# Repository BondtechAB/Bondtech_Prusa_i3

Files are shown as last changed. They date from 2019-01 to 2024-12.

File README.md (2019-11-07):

# Bondtech_Prusa_i3
Bondtech extruder upgrade for Prusa i3 printer uses 3:1 gearing ratio for improved precision and resolution, optimized geometry for the heat-sink cooling and many other improved features. With lower weight it also reduce vibrations and ghosting.

### Links
* Bondtech's Website: https://bondtech.se/en
* Assembly manual: https://support.bondtech.se/c/Prusa

### Contributors
This project was a Co-development with people from the Prusa community that have provided excellent feedback and suggestions of how to develop the "perfect" extruder setup for the Prusa series printer.

Special thanks to these aweome people! 
* Chris Warkocki
* Grégorie Saunier: https://github.com/gregsaun 
* Olof Ogland 
* Erik Bjorgan 
* Josh Jones 
* Kyle Wiehe 
* Marc Evertz 
* Matt Harrison 
* Ocie Ward
* Sando Bendig 
* Vecko Kojchevski 
* Steven Mölby

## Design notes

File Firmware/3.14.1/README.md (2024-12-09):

# 3.14.1 Firmware for Bondtech Prusa i3 MK25 / MK3,  MK25s / MK3s and MK25s / MK3s Mosquito

2024-12-09

Compiled firmware to support Bondtech Prusa i3 MK25 / MK3, MK25s / MK3s, MK25s / MK3s Mosquito and Bondtech LGX for MK3s & Mosquito

Firmware based on Prusa's latest release with adjustments to support bondtech extruders. Please read Prusa's release note for all changes in the new release: https://github.com/prusa3d/Prusa-Firmware/releases/tag/v3.14.1

# 3.14.1 Summary Bondtech specific changes

- Adjusted Load/Unload filament sequence.
- MK3/MK3s: Variants for Slice Engineering's High temperature thermistor (SE_HT-thermistor), E3DRevo.
- MK3/MK3s: Changed microstep resolution to 16.
- MK3s/MK25s: Correct Z_MAX_POS adjustments to allow XYZ Calibration.
- Full speed enabled for custom fans.

Source Code: https://github.com/BondtechAB/Bondtech-Prusa-Firmware

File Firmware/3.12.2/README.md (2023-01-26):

# 3.12.1 Firmware for Bondtech Prusa i3 MK25 / MK3,  MK25s / MK3s and MK25s / MK3s Mosquito

2023-01-26

Compiled firmware to support Bondtech Prusa i3 MK25 / MK3, MK25s / MK3s, MK25s / MK3s Mosquito and Bondtech LGX for MK3s & Mosquito

Firmware based on Prusa's latest release with adjustments to support bondtech extruders. Please read Prusa's release note for all changes in the new release: https://github.com/prusa3d/Prusa-Firmware/releases/tag/v3.12.1

# 3.12.1 Summary Bondtech specific changes

- Adjusted Load/Unload filament sequence.
- MK3/MK3s: Variants for Slice Engineering's High temperature thermistor (SE_HT-thermistor).
- MK3/MK3s: Changed microstep resolution to 16.
- MK3s/MK25s: Correct Z_MAX_POS adjustments to allow XYZ Calibration.
- MK3s/Mk25s: Adjusted mmu.cpp to correct values for E3Dv6, Mosquito and Mosquito Magnum together with the Bondtech extruder when preforming can_load and mmu_load_to_nozzle.
- Full speed enabled for custom fans.

Source Code: https://github.com/BondtechAB/Bondtech-Prusa-Firmware

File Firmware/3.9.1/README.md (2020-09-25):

# 3.9.1 Firmware for Bondtech Prusa i3 MK25 / MK3,  MK25s / MK3s and MK25s / MK3s Mosquito

2020-09-25

Compiled firmware to support Bondtech Prusa i3 MK25 / MK3, MK25s / MK3s, MK25s / MK3s Mosquito

Firmware based on Prusa's latest release with adjustments to support bondtech extruders. Please read Prusa's release note for all changes in the new release: https://github.com/prusa3d/Prusa-Firmware/releases/tag/v3.9.1

# 3.9.1 Summary Bondtech specific changes

- Variants for Slice Engineering's High temperature thermistor (SE_HT-thermistor).
- Adjusted Load/Unload filament sequence.
- MK3/MK3s: Changed microstep resolution to 16.
- MK3s/MK25s: Correct Z_MAX_POS adjustemts to allow XYZ Calibration.
- MK3s/Mk25s: Adjusted mmu.cpp to correct values for E3Dv6, Mosquito and Mosquito Magnum together with the Bondtech extruder when preforming can_load and mmu_load_to_nozzle.
- Now with multi language support.
- Full speed enabled for custom fans.

Source Code: https://github.com/BondtechAB/Bondtech-Prusa-Firmware

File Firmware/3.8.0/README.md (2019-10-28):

# 3.8.0 Firmware for Bondtech Prusa i3 MK25 / MK3,  MK25s / MK3s and MK25s / MK3s Mosquito

2019-09-11

Compiled firmware to support Bondtech Prusa i3 MK25s / MK3s, MK25s / MK3s Mosquito

# Summery Bondtech specific changes

- Variants for Slice Engineerings High temperature thermistor (SE_HT-thermistor)
- Adjusted Load/Unload filament sequence
- MK3/MK3s: Changed mirostep resolution to 16
- MK3s/MK25s: Changed Z_MAX_POS 205 to allow Z and XYZ calibration

##  MK3s Changes

- #define CUSTOM_MENDEL_NAME "Bondtech-PE MK3s"
- #define DEFAULT_AXIS_STEPS_PER_UNIT   {100,100,3200/8,415}
- #define Z_MAX_POS 205
- #define TMC2130_USTEPS_E    16    
- #define LOAD_FILAMENT_1 "G1 E80 F400"
- #define UNLOAD_FILAMENT_1 "G1 E-95 F7000"
- #define FILAMENTCHANGE_FINALRETRACT -95
- #define FILAMENTCHANGE_FIRSTFEED 80  

## MK3 Changes

- #define CUSTOM_MENDEL_NAME "Bondtech-PE MK3"
- #define DEFAULT_AXIS_STEPS_PER_UNIT   {100,100,3200/8,415}
- #define TMC2130_USTEPS_E    16
- #define LOAD_FILAMENT_1 "G1 E80 F400"
- #define UNLOAD_FILAMENT_1 "G1 E-95 F7000"
- #define FILAMENTCHANGE_FINALRETRACT -95
- #define FILAMENTCHANGE_FIRSTFEED 80

##  MK25s Changes

- #define CUSTOM_MENDEL_NAME "Bondtech-PE MK2.5S"
- #define DEFAULT_AXIS_STEPS_PER_UNIT   {100,100,3200/8,415}
- #define LOAD_FILAMENT_1 "G1 E80 F400"
- #define UNLOAD_FILAMENT_1 "G1 E-95 F7000"
- #define FILAMENTCHANGE_FINALRETRACT -95
- #define FILAMENTCHANGE_FIRSTFEED 80

## MK25 Changes

- #define CUSTOM_MENDEL_NAME "Bondtech-PE MK2.5"
- #define DEFAULT_AXIS_STEPS_PER_UNIT   {100,100,3200/8,415}
- #define LOAD_FILAMENT_1 "G1 E80 F400"
- #define UNLOAD_FILAMENT_1 "G1 E-95 F7000"
- #define FILAMENTCHANGE_FINALRETRACT -95
- #define FILAMENTCHANGE_FIRSTFEED 80

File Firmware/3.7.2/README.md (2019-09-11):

# bondtech_fw_MK3S_3_7_2.hex for MK3s

2019-07-12

Compiled firmware to support Bondtech Prusa i3 MK3s.

# Bondtech specific changes
1. Estep set to 830.
2. Z_MAX_POS 204 to allow Z and XYZ calibration.
3. Changed printer name.

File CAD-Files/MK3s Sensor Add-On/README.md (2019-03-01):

You can find the assembly manual here.

https://github.com/BondtechAB/Bondtech_Prusa_i3/blob/master/Doc/Sensor%20Add-On%20V1.0.pdf

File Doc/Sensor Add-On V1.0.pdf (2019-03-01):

# Sensor Add-On for Bondtech Prusa i3

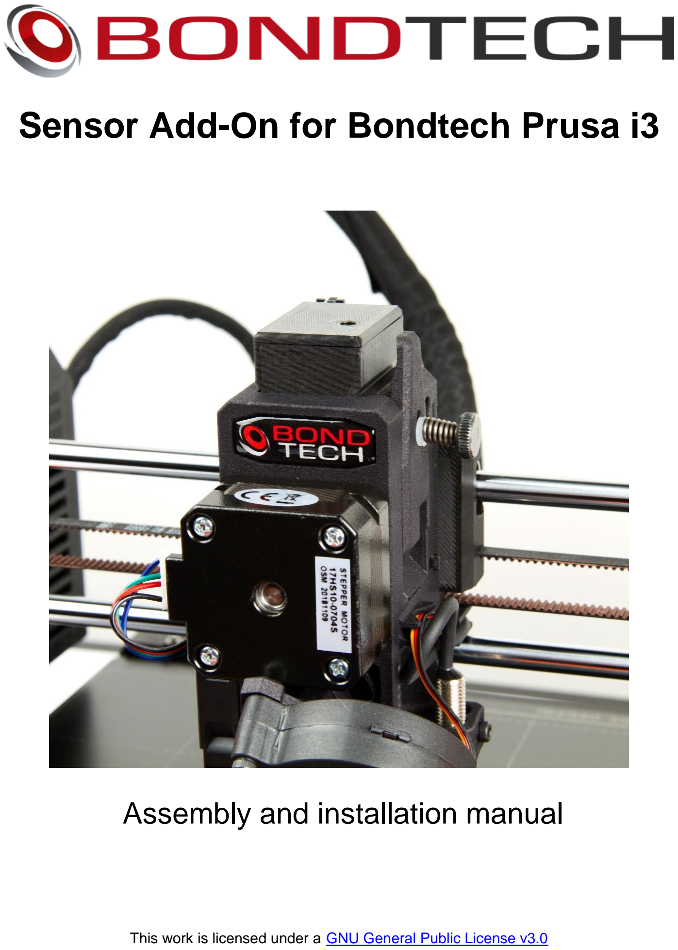
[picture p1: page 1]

## Assembly and installation manual

This work is licensed under a GNU General Public License v3.0 (https://www.gnu.org/licenses/gpl-3.0.html)

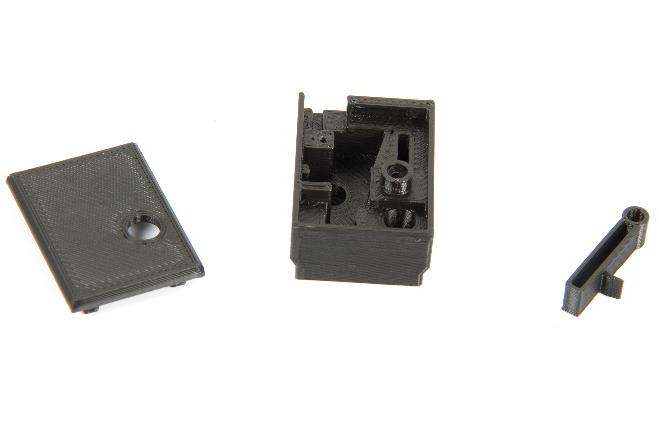
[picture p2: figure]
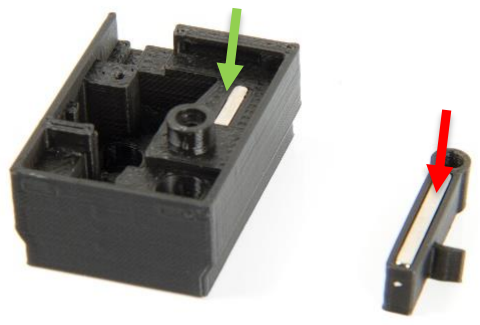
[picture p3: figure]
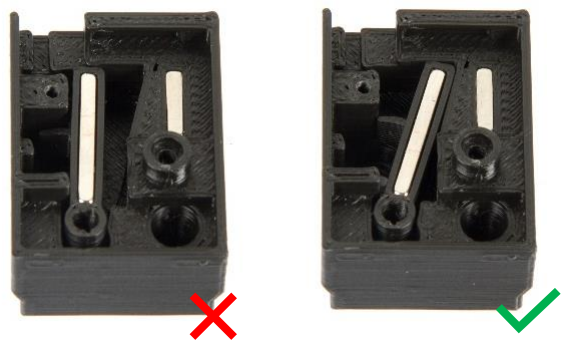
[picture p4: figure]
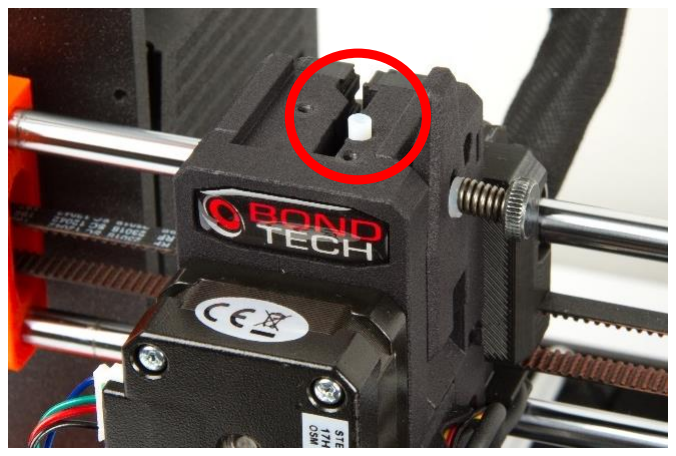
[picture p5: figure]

Installation of Sensor Add-On for Bondtech_Prusa_i3 V1.0 | 1
- Preparation. Download and print the lever, housing and cover from our GitHub page.
https://github.com/BondtechAB/Bondtech_Prusa_i3/tree/master/C AD-Files (https://github.com/BondtechAB/Bondtech_Prusa_i3/tree/master/CAD-Files)
- Recommended to print the lever with extra flow if the magnet is loose in the pocket.
- Insert the magnet. Make sure the 20x6x2 magnet is securely held in the lever.
- 20x6x2 magnet
- 10x6x2 magnet
- Ensure the magnets are
attracting each other.
- Remove your old sensor cover.
- Cut your old PTFE tube 6,5mm, chamfer the inside and insert it into the extruder body.

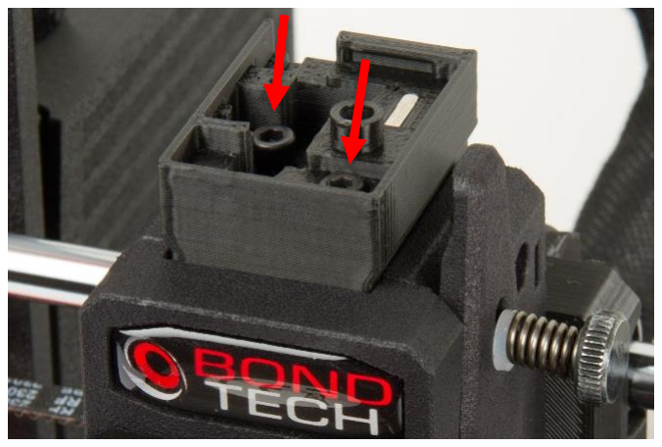
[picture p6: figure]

- Insert the new sensor housing in the slot and secure it using two M3x8 screws.
- M3x8

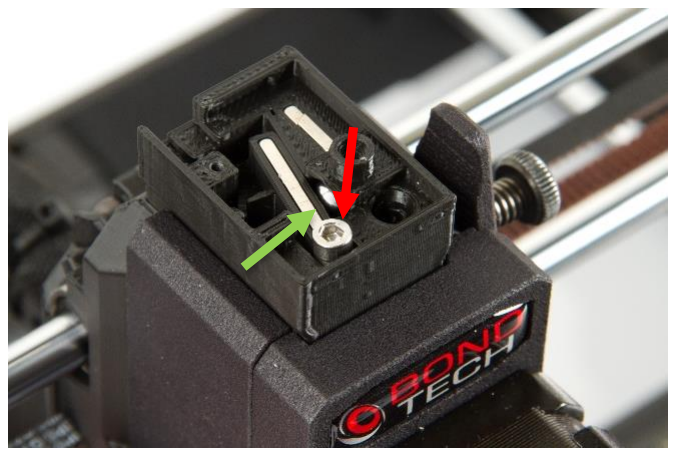
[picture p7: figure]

- Insert the steel ball and lever. Secure the lever using a M3x10 screw from your upgrade kit. (Make sure the lever can move freely)
- Steel ball
- M3x10

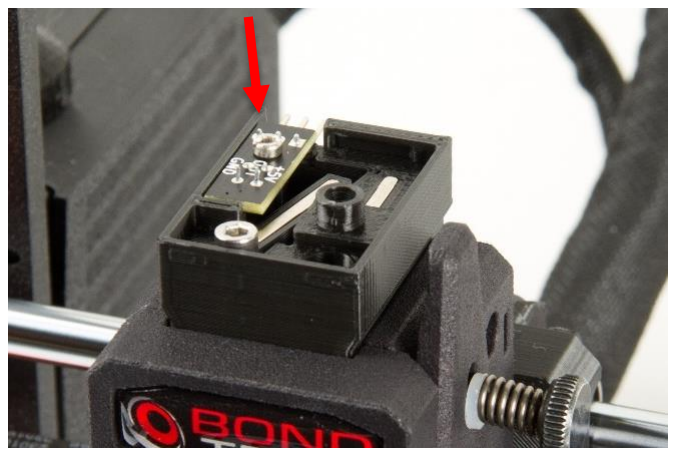
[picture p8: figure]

- Place and secure the sensor with a M2x8 screw delivered in your MK3s upgrade kit.
- M2x8

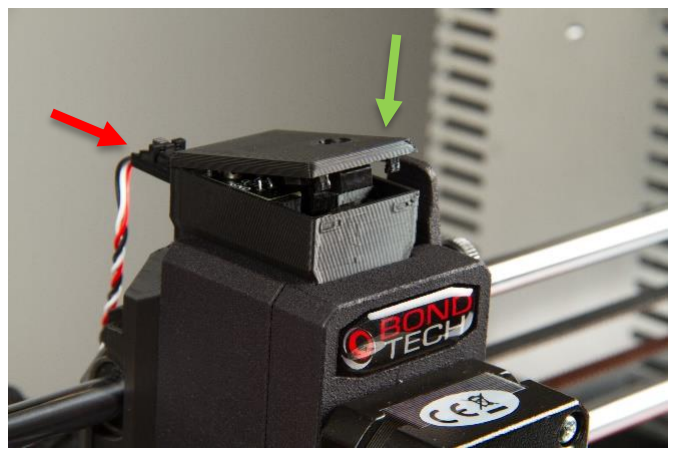
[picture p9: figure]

- Slide the lid back and carefully push it down in the front.
- Connect the wire to the sensor.

Good luck with your Bondtech feeder!

If you have any questions please first read the FAQ (http://www.bondtech.se/en/faq/). If the question still hasn’t been answered feel free to contact us by email or our online chat.

Repslagarvägen 3 J
33153 Värnamo
Sweden

e-mail: support@bondtech.se phone: +46702220193
paypal: payments@bondtech.se
web: www.bondtech.se
VAT-registration number: SE556995564301

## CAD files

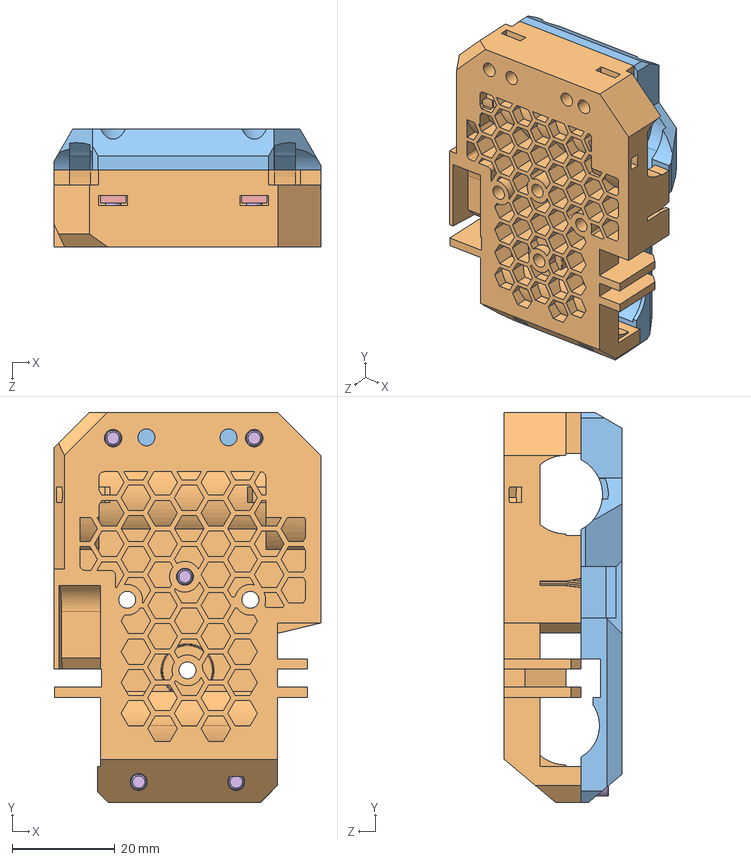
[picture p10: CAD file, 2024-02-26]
CAD-Files/Bondtech LGX for MK3S & Mosquito/LGX X-carriage for MK3S & Mosquito.STEP
52.0 x 76.0 x 22.9 mm
FKM Fyrkantsmutter_FKM2.5 x 5
MC6S_M3X10OBEH x 5

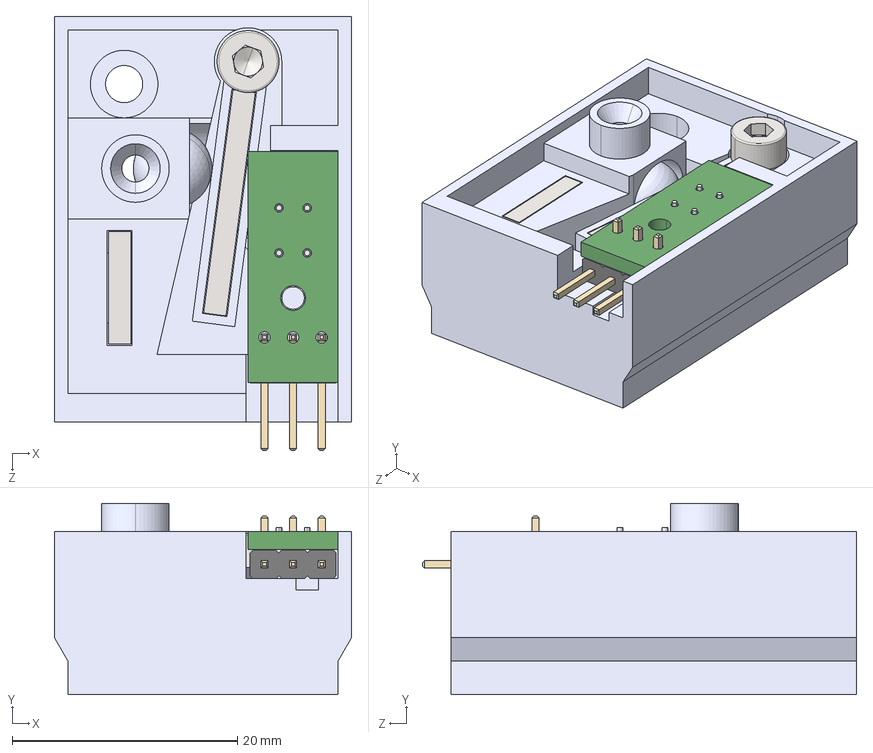
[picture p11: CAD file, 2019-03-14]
CAD-Files/MK3s Sensor Add-On/MK3s Sensor Add-On.STEP
26.4 x 17.0 x 38.5 mm
Magnet 10x6x2
Magnet 20x6x2
IR-sensor_Part
Sensor Housing
Kula 7mm
socket head cap screw_iso_ISO 4762 M3 x 10 - 10N
Lever.2.1

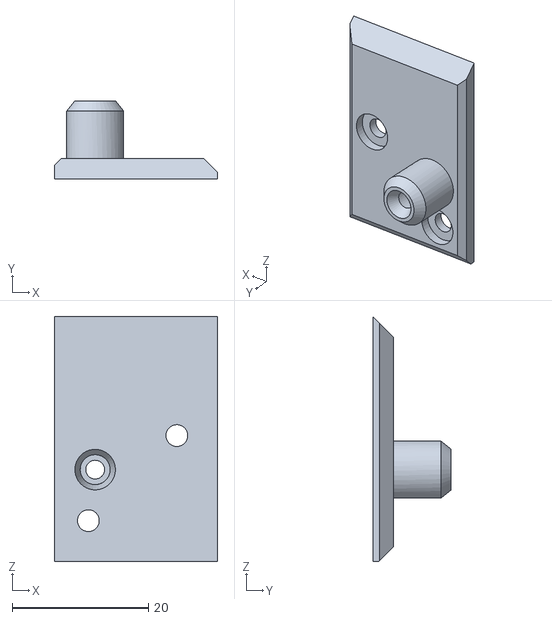
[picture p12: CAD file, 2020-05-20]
CAD-Files/Sensor Cover MK2-MK2s_MK2.5-MK3.STL
24.0 x 11.5 x 36.0

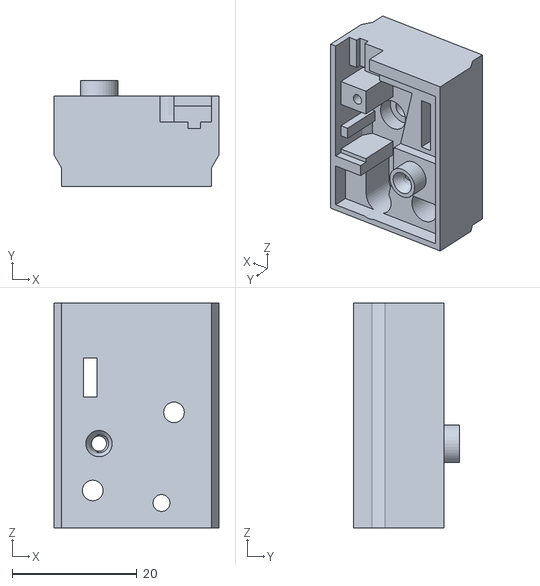
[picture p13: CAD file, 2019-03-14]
CAD-Files/MK3s Sensor Add-On/Sensor Housing.STL
26.4 x 17.0 x 36.0

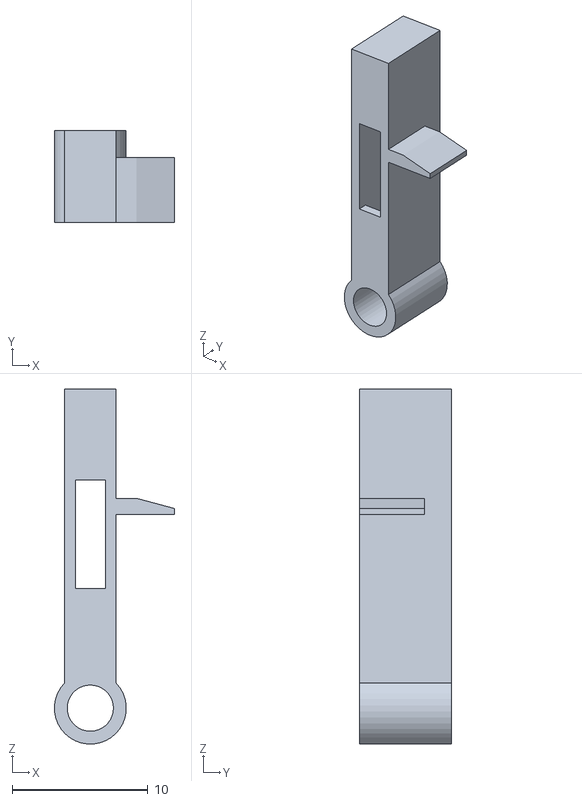
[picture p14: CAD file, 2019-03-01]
CAD-Files/MK3s Sensor Add-On/Lever.STL
8.84 x 6.80 x 26.1

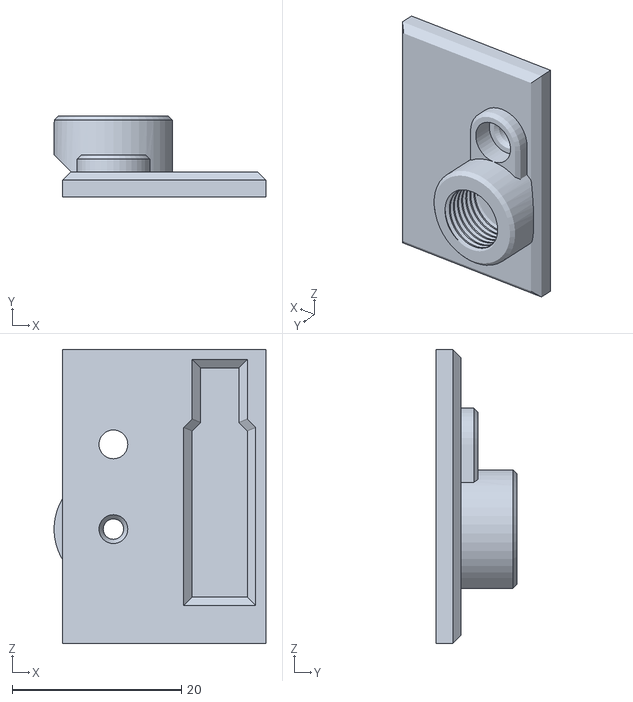
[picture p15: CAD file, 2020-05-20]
CAD-Files/Sensor Cover MK3s-1-8in_thread.STL
25.0 x 9.60 x 34.7

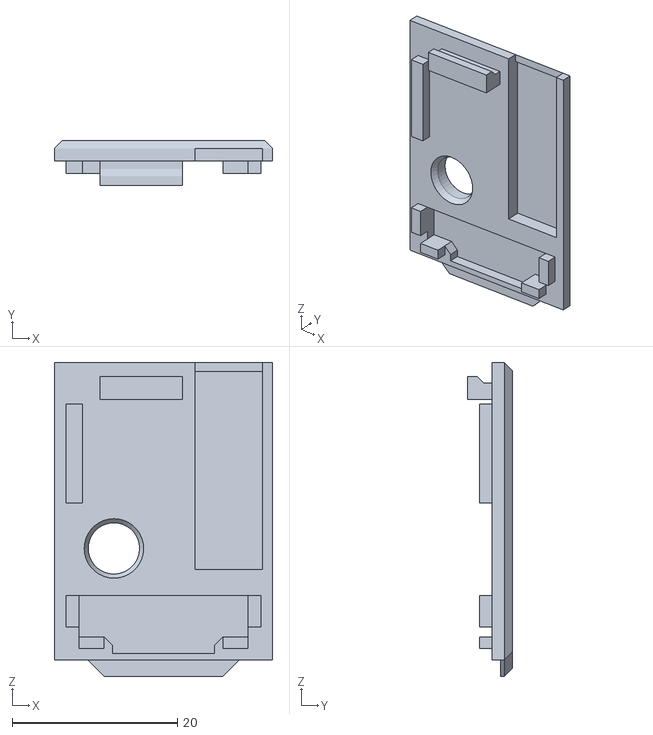
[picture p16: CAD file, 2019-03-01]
CAD-Files/MK3s Sensor Add-On/Sensor Cover.STL
26.4 x 5.50 x 38.0

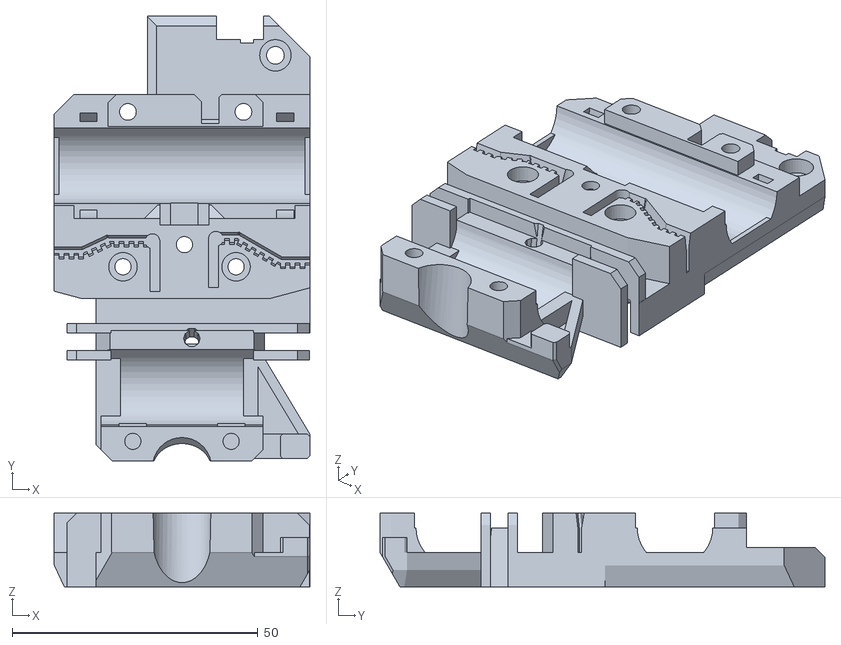
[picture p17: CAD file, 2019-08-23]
CAD-Files/X-carriage(R2)_Bondtech_MK2.5s.STL
52.0 x 90.5 x 15.0

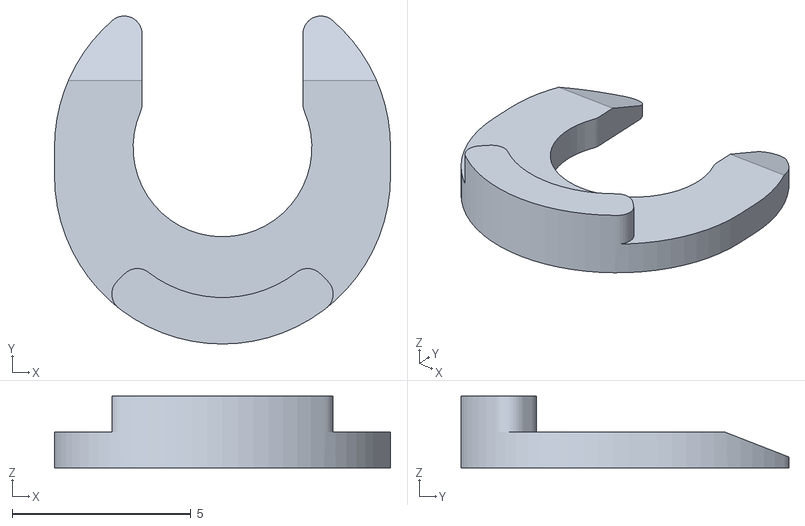
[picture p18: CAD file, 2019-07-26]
CAD-Files/Bowden-clip 1.75.STL
9.40 x 9.17 x 2.00

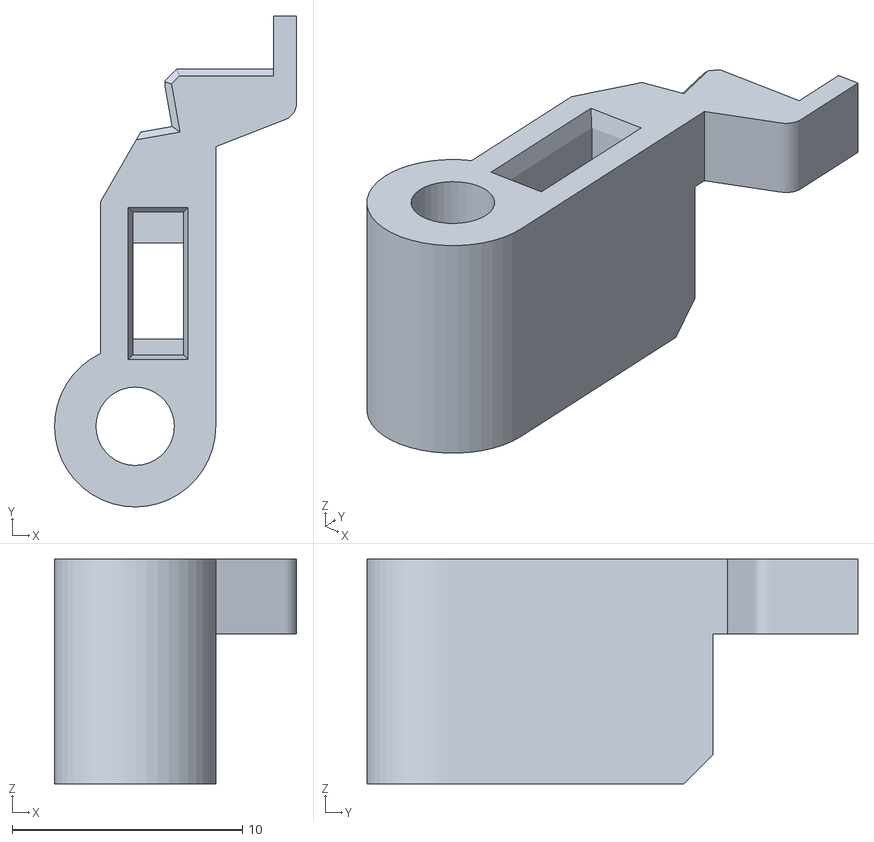
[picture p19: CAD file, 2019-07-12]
CAD-Files/fs-lever_1.1.STL
10.5 x 21.3 x 9.75

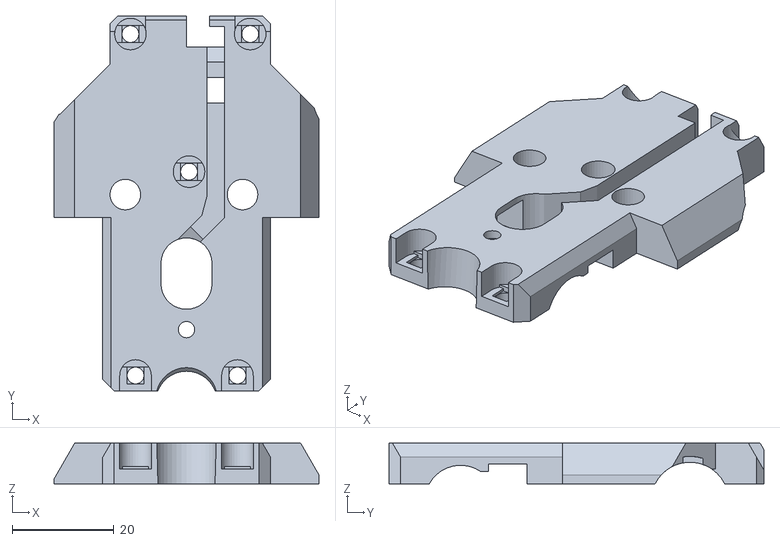
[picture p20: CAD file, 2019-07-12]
CAD-Files/Prusa X-Carriage Rear (R3).STL
52.0 x 73.5 x 8.00

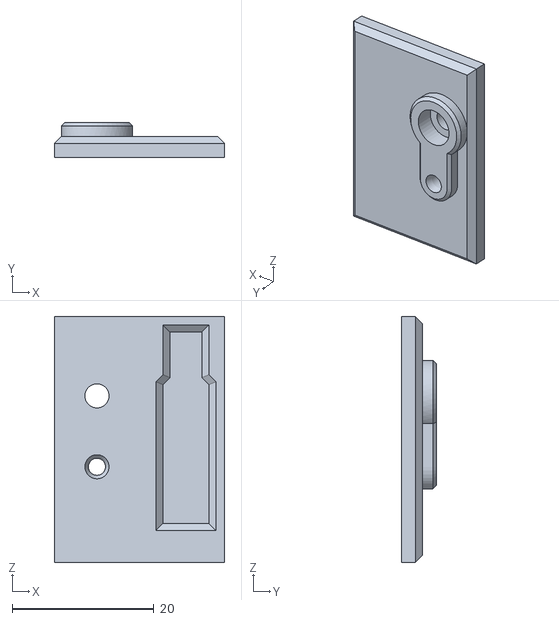
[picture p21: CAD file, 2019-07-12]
CAD-Files/Sensor Cover MK3s.STL
24.0 x 5.00 x 34.7

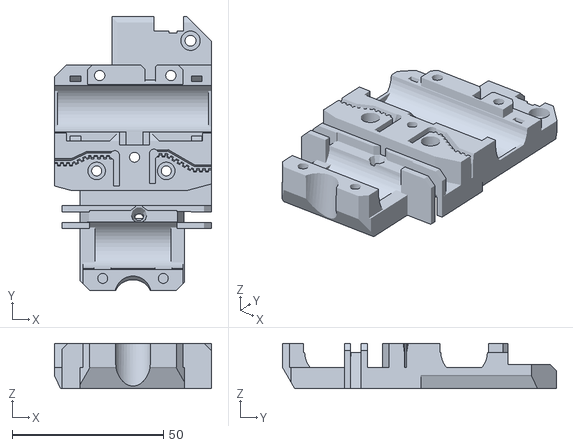
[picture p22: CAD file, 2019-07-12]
CAD-Files/X-carriage(R2)-MK3s.STL
52.0 x 90.5 x 15.0

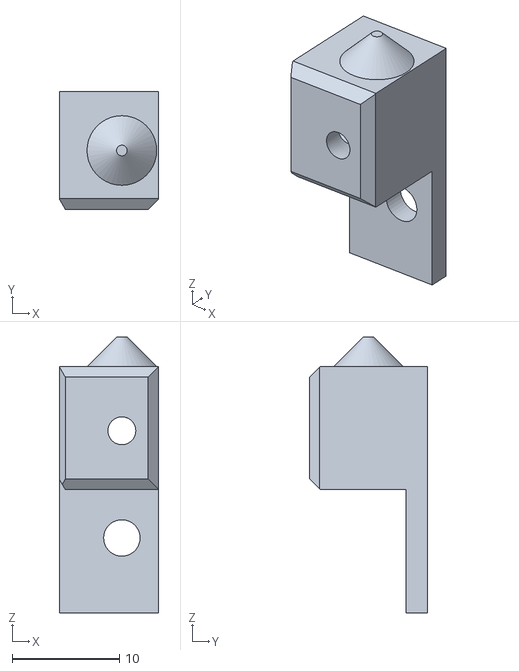
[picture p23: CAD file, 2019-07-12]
CAD-Files/adapter-printer.v1.1.STL
9.20 x 11.0 x 25.8

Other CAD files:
CAD-Files/Sensor Cover MK3s-M6x1.STL
CAD-Files/Sensor Cover MK3s-M5x0,8.STL
CAD-Files/X-Carriage-modded(R2)__for_MK2(s).STL
CAD-Files/PTFE-CUTTER_1.0.STL

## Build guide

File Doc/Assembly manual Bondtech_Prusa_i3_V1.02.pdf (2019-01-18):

# Bondtech for Prusa i3

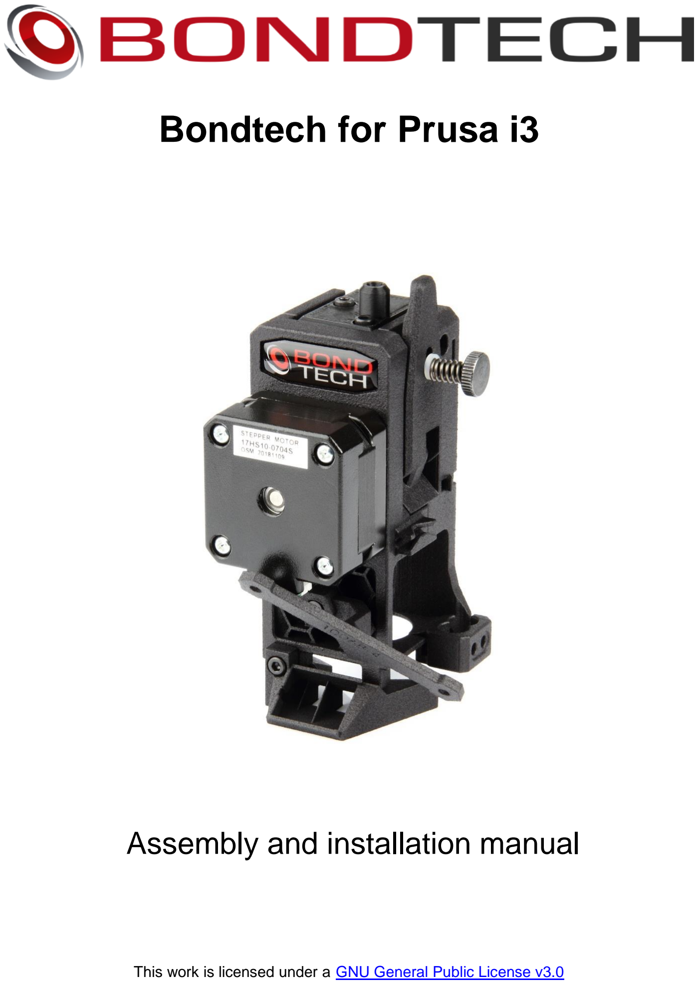
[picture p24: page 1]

## Assembly and installation manual

This work is licensed under a GNU General Public License v3.0 (https://www.gnu.org/licenses/gpl-3.0.html)

Installation manual extruder upgrade for Bondtech_Prusa_i3 V1.02

## Table of Contents

Acknowledgements | 1
Introduction | 1
Compatibility | 2
What’s in the box? | 2
Mechanical Installation | 3
What you need | 3
Preparation | 3
Software Configuration | 15
Set new E-step value | 15

## Acknowledgements

This is a co-development work with awesome guys in the Prusa Community like Chris Warkocki, Grégorie Saunier (Bear Upgrades), Olof Ogland, Erik Bjorgan, Josh Jones, Kyle Wiehe, Marc Evertz, Matt Harrison, Ocie Ward, Sando Bendig, Vecko Kojchevski (Vecko Extruder), Steven Mölby that have provided excellent feedback and suggestions of how to develop the "perfect" extruder setup for the Prusa series printer. A lot of work has been spent in this project and we have tried to listen to all the inputs in order to find a solution that can be fitted to a Prusa I3 MK2, MK2S, MK2.5 and MK3.

## Introduction

This kit contains the necessary parts to convert to our freshly designed extruder that uses 3:1 gearing ratio for improved precision and resolution, optimized geometry for the heat-sink cooling and many other improved features.
It also reduces the moving weight to reduce vibrations and ghosting.

## Compatibility

The upgrade is compatible with the following machines:

- Prusa i3 MK2
- Prusa i3 MK2s
- Prusa i3 MK2,5
- Prusa i3 MK3

## What’s in the box?

All customers

1x Bondtech extruder for Prusa i3. 1x PTFE tube (80mm).
1x SLS printed Extruder front.
1x SLS printed Extruder rear.
1x Bag with screws and bolts. 1x Fan shroud.
1x Mounting bracket.

MK2, MK2s, MK2.5 and MK3 without BMG

1x Nema17 Pancake stepper motor.
1x Stepper motor cable.
1x Shaft with 50T gear.
1x Thumbscrew.
2x Ball bearings.
1x 3x32mm shaft.
1x Sensor cover

MK2 and Mk2s

2x Needle bearing.
1x 3x20mm shaft.
1x Primary drive wheel (direct). 1x Secondary drive wheel (direct). 1x Sensor cover

## Mechanical Installation

## What you need

To install the upgrade you will need.
- M1.5- Hex Wrench
- M2.5- Hex Wrench
- Hobby knife with sharp tip or similar.

Recommended: Download and print out Bondtech’s PTFE fixture for precise measurement of the tube length. STL-file available at https://github.com/BondtechAB/Bondtech_Prusa_i3/tree/master/CAD-Files

## Preparation

Remove your old extruder. Use Prusa’s extruder assembly guide to reverse the steps if you need to. This kit will use a different motor, so you can unwrap the cables, remove your current motor to prepare for a new one.

- Preparing your motor.

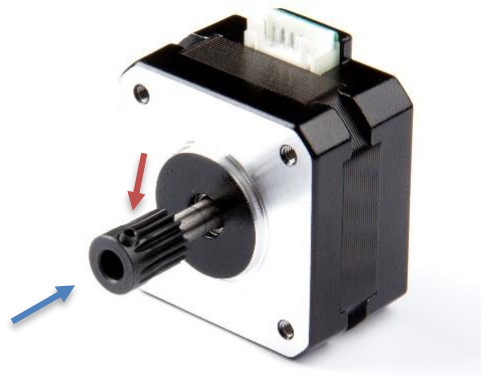
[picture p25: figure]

- Insert the M2x3 setscrew and slide the motor gear onto the shaft as oriented in the picture.

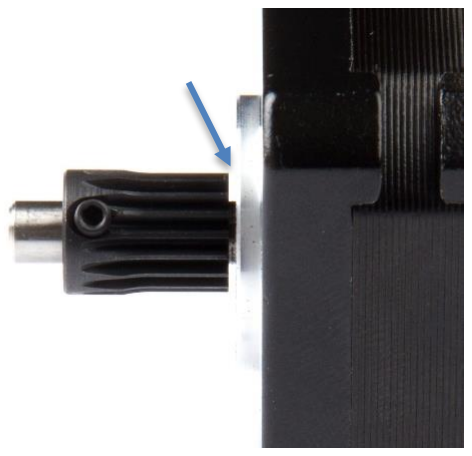
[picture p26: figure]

- Leave a 1-1,5 mm gap between the gear and the motor and tighten it using your 1,5mm Allen key.

Recommended: Use Loctite to secure the screw.

- Assembly the extruder front. Make sure the pre-assembled M3 Hex nut is mounted and fixed in the front piece of the extruder body.

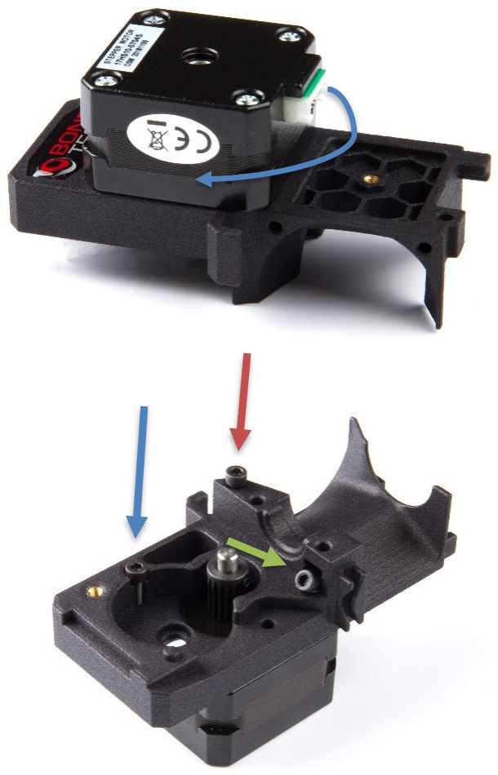
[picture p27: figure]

- Place the motor on the extruder front and orient the cable connection as you choose.
(Downwards or to the left.)

- Insert three M3 screws and loosely tighten them using a 2.5mm Allen key.
- M3x8
- M3x12
- M3x25

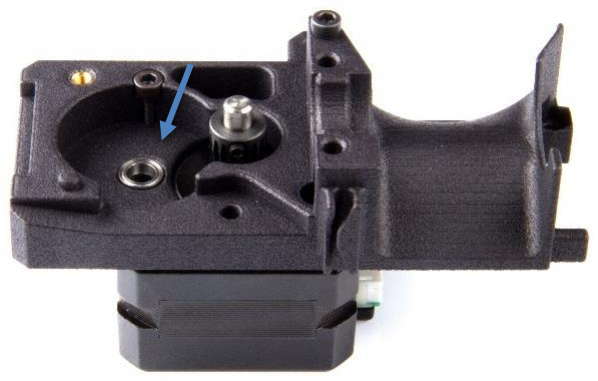
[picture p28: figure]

- Insert a ball bearing. Ensure it is fully pressed down into the slot.
- Insert the shaft with the white plastic gear into the bearing. Rotate the shaft to ensure correct alignment of the gears.

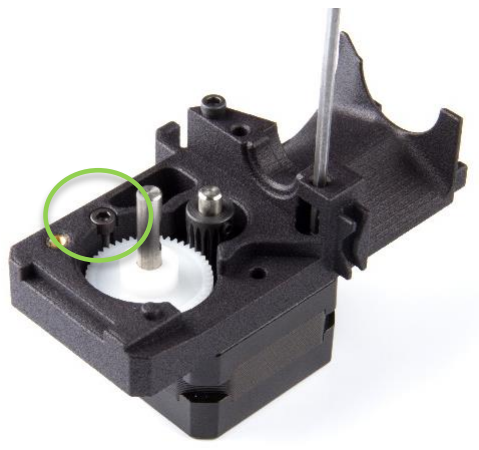
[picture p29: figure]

- Tighten the screws with
reasonable force.
- Important: Be careful
when tighten the M3x12
screw to avoid damaging
the pocket!

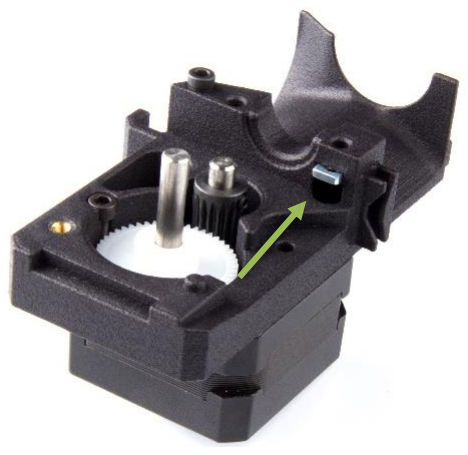
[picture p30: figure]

- Insert a square nut into the pocket.
- Prepare the extruder rear. Insert a ball bearing and press it down using a primary drive gear.
- If you are using the bear X-carriage remove hex cover plug by pushing it from the rear side. This hole is for a M3 nut.

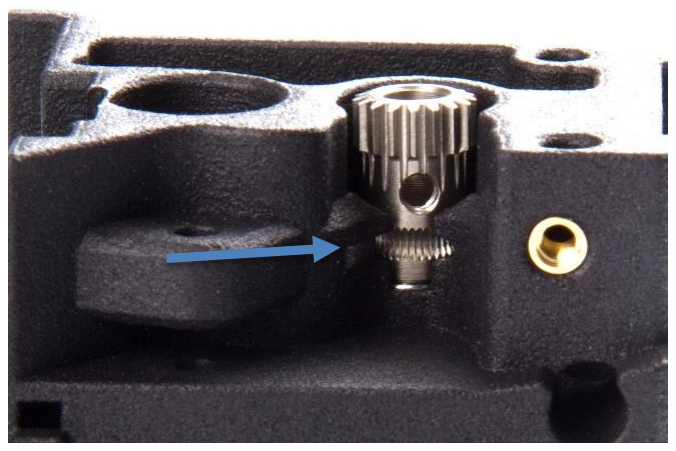
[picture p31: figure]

- Press the primary drive gear down until the groves align with the filament path.

- Slide the shaft inside the drive gear. Note the orientation of the parts. The hole and the flat surface on the shaft must align.

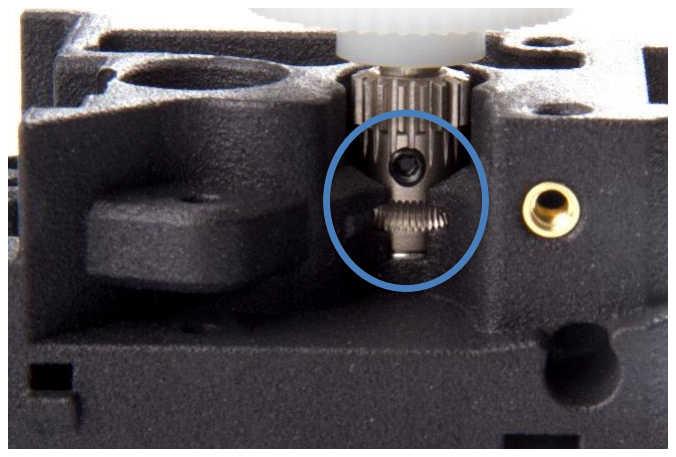
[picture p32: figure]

- Insert the M3x2 setscrew and tighten it with your 1,5 Allen key.

Important: Ensure the groves align with the filament path!

Recommended: Use Loctite to secure the screw.

Important: If the setscrew is not properly aligned with the flat surface it will stick out and start grinding on the
secondary drive gear when you start printing!

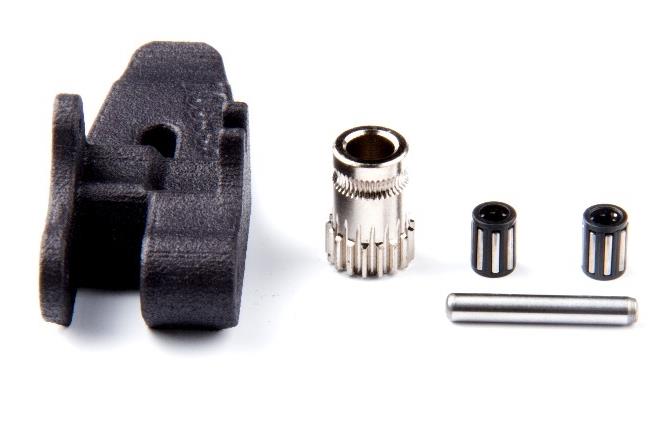
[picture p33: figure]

- Assemble the hinge.

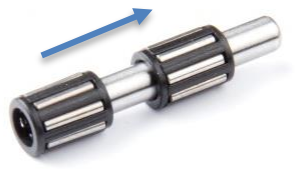
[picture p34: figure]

- Slide the two needle bearings onto the 3x20 mm shaft.
- Use a small dab of lithium based grease to lubricate the bearings
- Slide the shaft with the bearings through the secondary drive gear.
- Align the gear with the hinge as shown in the photo and press the shaft down until you hear the click.
- Carefully press the shaft in place using your 2.5mm Allen key.
- Put a small dab of lithium based grease on the gear section to reduce friction. Make sure that you do not get it on the drive section of the gear.

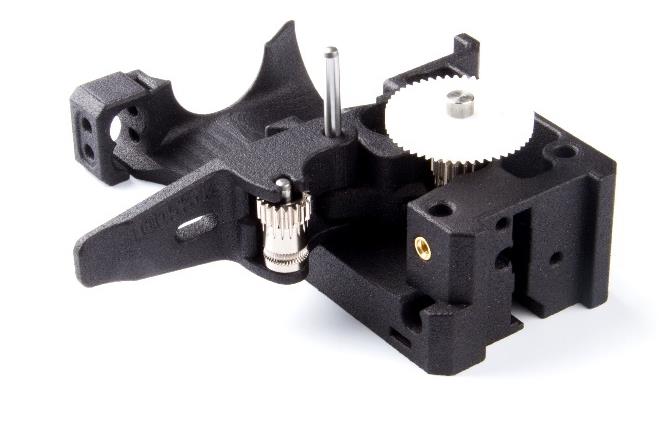
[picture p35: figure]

- Install the hinge to the extruder rear using the 3x32mm shaft.

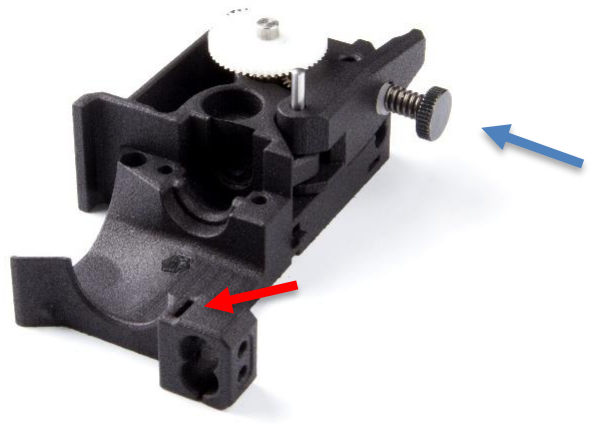
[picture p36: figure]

- Install the thumbscrew.
- If you are a MK2/s user
insert a square nut in the front pocket for the Pinda Probe.
- Prepare the HotEnd. Take the new supplied PTFE tube. Cut one of the ends according to Prusas recommendation, using a knife or a razor. Using this fixture (https://www.thingiverse.com/thing:3344656) will help. (Credits to Olof Ogland)
- Insert the newly cut end of the tube into the HotEnd.

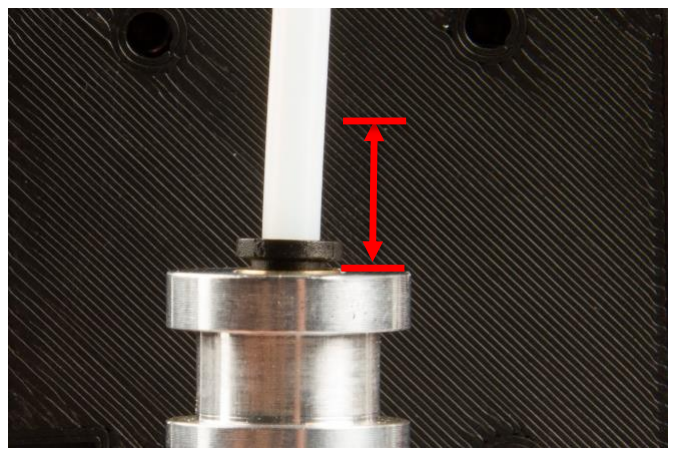
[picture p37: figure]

- Cut the tube 6.3 mm from the top of the HotEnd. Save the
remaining piece for the sensor cover.

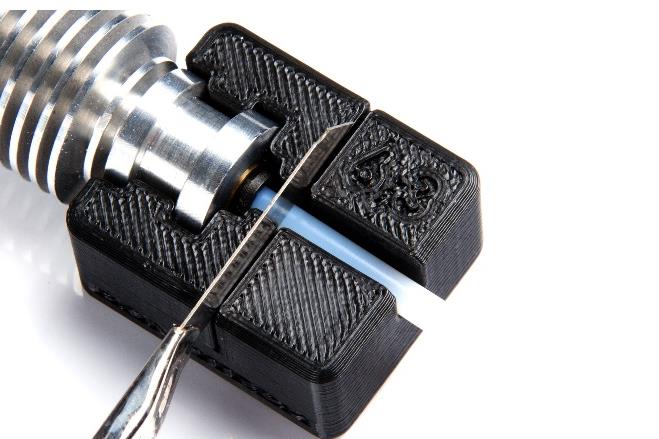
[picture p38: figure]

- Recommended: Use Bondtech’s cutting fixture for precise measurement. STL-file is
available at:
https://github.com/BondtechAB/Bondtech_Prusa_i3/tree/master/C AD-Files (https://github.com/BondtechAB/Bondtech_Prusa_i3/tree/master/CAD-Files)
- Use a knife or razor to chamfer the inside of the tube for better filament guidance.

Important: Do not let any left over from the tube fall into the HotEnd we recommend you
remove the tube before
chamfer the inside!
- Insert a push fit clip between the HotEnd and the collet.
- Recommended: Add a small piece of tape, 5x20mm on the inner ring. The low friction between the parts may cause the HotEnd to rotate to easily when installed.

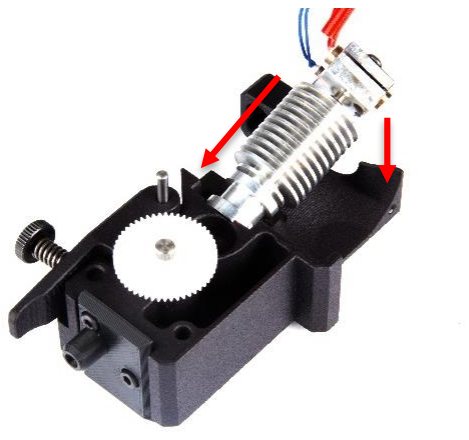
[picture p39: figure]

- Install the HotEnd into the extruder rear, angled as shown in the photo. And push it in place.

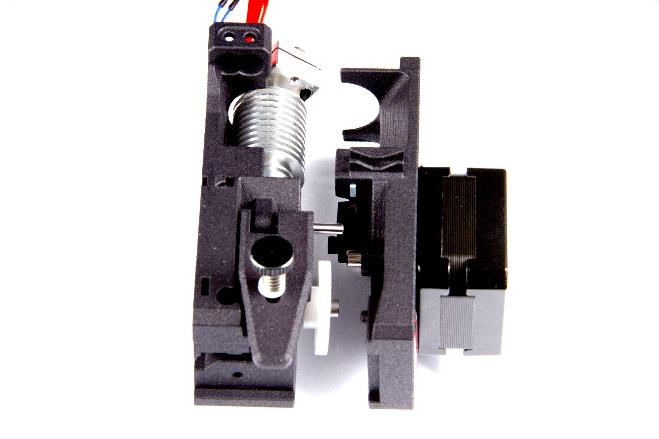
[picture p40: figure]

- Attach the front onto the rear part. Push the HotEnd upwards to align the neck correctly.
- Ensure everything is aligned and carefully clamp the parts
together.

Important: The parts should fit together easy. Do not use any excessive force!

- Install the extruder to your X-Carriage using three M3 screws.
- M3x40
- M3x45

Important: These screws are sized to use on your stock MK2,5/MK3 carriage or the
modified MK2/s carriage. If you have another carriage different screw length could be
necessary!

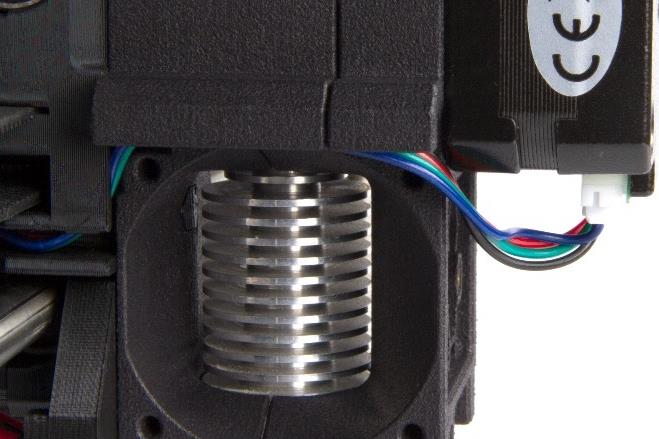
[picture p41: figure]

- Connect the cable to the motor and use the cable path to the left of the extruder for guidance.

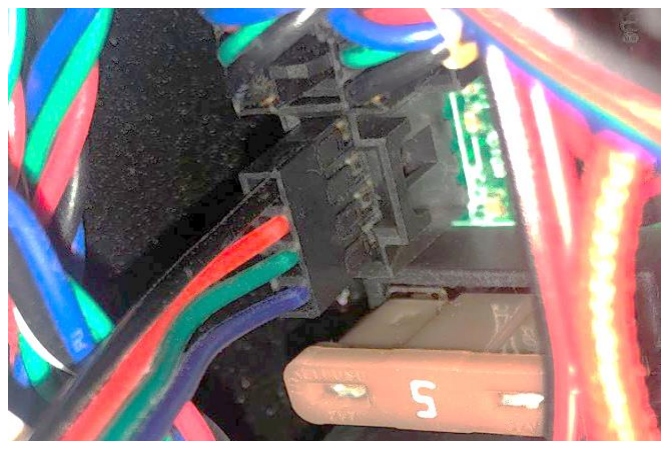
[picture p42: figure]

- When connecting the cable to you board ensure the black cable is the top most cable or the motor will rotate the wrong way!

- Install your 40x40 fan using four M3x12 screws.

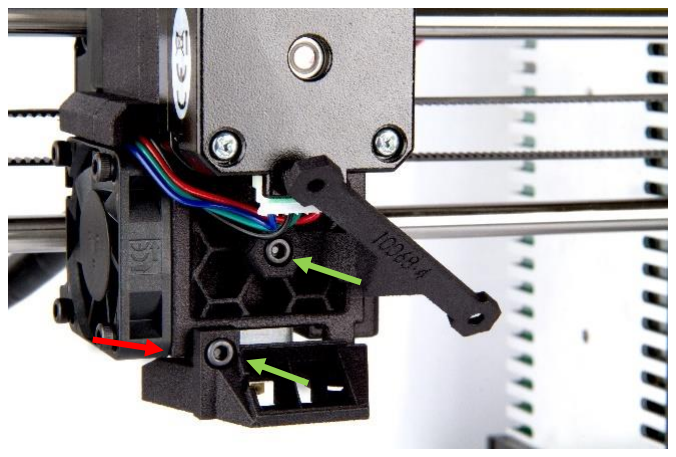
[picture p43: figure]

- Install the mounting bracket using a M3x10 screw. Place a M3 hex nut in the pocket and tightened the fan shroud using a M3x10 screw.
- M3x10
- M3 hex nut

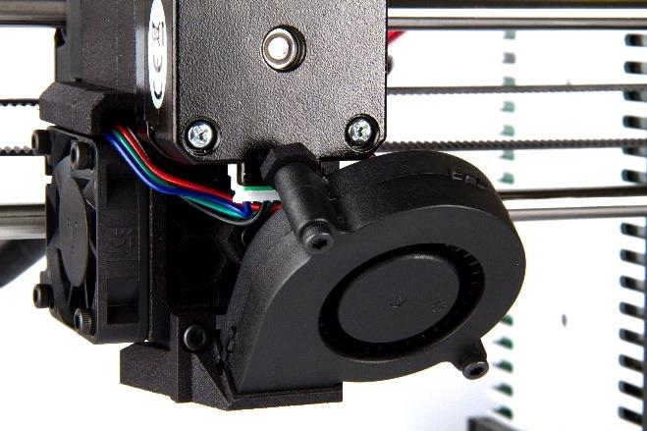
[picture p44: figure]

- Place two hex nuts into the slots on the mounting bracket and slide your 5015-blower fan down the fan shroud and mount it using two M3x20 screws.
- Place the cable in the channel on the right side of the extruder to help guide the way.
- The position of the P.I.N.D.A probe depends on your version of the printer. MK2/s users place the probe to right (Closer to the X-axis) MK2.5 and MK3 users place the probe to the left (furthest away from the X-axis).

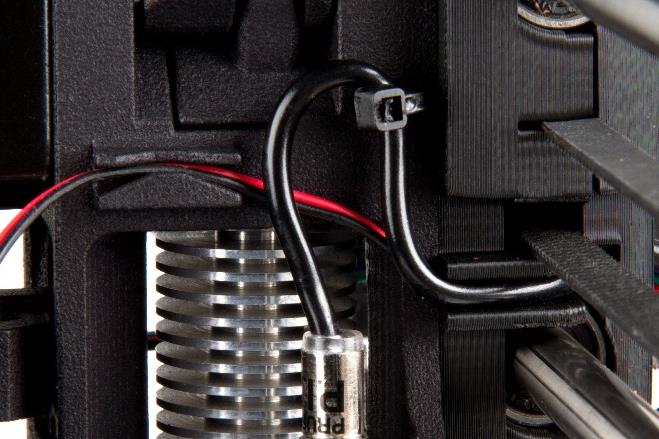
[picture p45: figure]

- Optional P.I.N.D.A cable position. This technique is developed by Grégoire Saunier, creator of the Bear Extruder, to improve air flow and reduce turbulence. Check out his work here: (https://github.com/gregsaun)

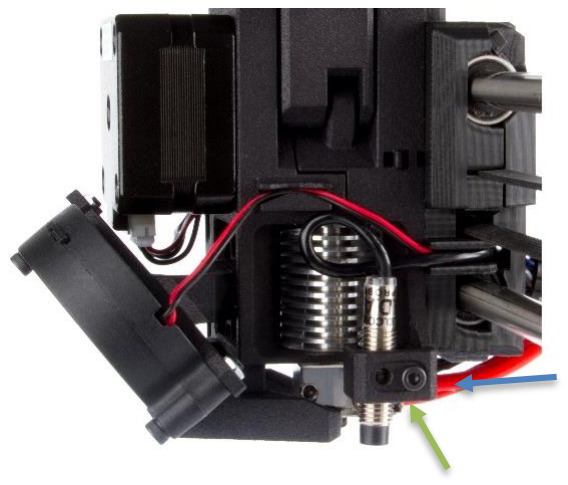
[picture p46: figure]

- MK2.5, MK3 users insert a square nut into the right slot (MK2s in the left as shown earlier). Secure the P.I.N.D.A using a M3x16 screw.
- Square nut
- M3x16

Reminder: Adjust the height of the probe according to Prusa’s instructions.

- Cut a 14.5mm long piece of the left-over PTFE Tube and insert it into the filament path on top of the extruder.

Recommended: Before inserting the tube use a knife or razor to chamfer the inside of the tube for better filament guidance.

- If you have a filament sensor install it according to Prusa’s instructions.

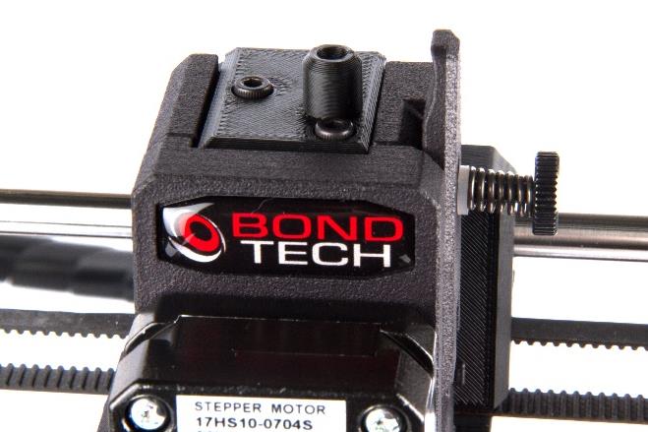
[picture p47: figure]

- Place the sensor cover on top and fasten it using two M3x8 screws.

## Software Configuration

As the new extruder uses a gear reduction to create a high extrusion resolution and high torque the E-step value needs to be changed. The E-step value tells the printer how many steps to send to the motor for each mm of filament.

## Set new E-step value

The E-step value is set using a G-code file that you can download here: (https://github.com/BondtechAB/Bondtech_Prusa_i3/tree/master/GCODE)
These files are used to set the new E-step value on the printer. On MK2, MK2S and MK2.5 the E-step value should be 415 as it uses 16-bit microstepping, on MK3 it shall be 830 as it uses 32-bit microstepping, this is valid for standard 1.8 degree stepper motors, if a 0.9 degree motor is used the E-step needs to be doubled, so 830 and 1660.

Copy the file to the SD-card and put it in the printer, select to print the file and the new e-step value will be set and saved to the controller.

Good luck with your Bondtech feeder!

If you have any questions please first read the FAQ (http://www.bondtech.se/en/faq/). If the question still hasn’t been answered feel free to contact us by email or our online chat.

Repslagarvägen 3 J
33153 Värnamo
Sweden

e-mail: support@bondtech.se phone: +46702220193
paypal: payments@bondtech.se
web: www.bondtech.se
VAT-registration number: SE556995564301

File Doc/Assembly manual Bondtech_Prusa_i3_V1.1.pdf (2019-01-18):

# Bondtech for Prusa i3


## Assembly and installation manual

This work is licensed under a GNU General Public License v3.0 (https://www.gnu.org/licenses/gpl-3.0.html)

Installation manual extruder upgrade for Bondtech_Prusa_i3 V1.1 | 1

## Table of Contents

Acknowledgements | 1
Introduction | 1
Compatibility | 2
What’s in the box? | 2
Mechanical Installation | 3
What you need | 3
Preparation | 3
Software Configuration | 15
Set new E-step value | 15

## Acknowledgements

This is a co-development work with awesome guys in the Prusa Community like Chris Warkocki, Grégorie Saunier (Bear Upgrades), Olof Ogland, Erik Bjorgan, Josh Jones, Kyle Wiehe, Marc Evertz, Matt Harrison, Ocie Ward, Sando Bendig, Vecko Kojchevski (Vecko Extruder), Steven Mölby that have provided excellent feedback and suggestions of how to develop the "perfect" extruder setup for the Prusa series printer. A lot of work has been spent in this project and we have tried to listen to all the inputs in order to find a solution that can be fitted to a Prusa I3 MK2, MK2S, MK2.5 and MK3.

## Introduction

This kit contains the necessary parts to convert to our freshly designed extruder that uses 3:1 gearing ratio for improved precision and resolution, optimized geometry for the heat-sink cooling and many other improved features.
It also reduces the moving weight to reduce vibrations and ghosting.

Installation manual extruder upgrade for Bondtech_Prusa_i3 V1.1 | 2

## Compatibility

The upgrade is compatible with the following machines:

- Prusa i3 MK2
- Prusa i3 MK2s
- Prusa i3 MK2,5
- Prusa i3 MK3

## What’s in the box?

All customers

1x Bondtech extruder for Prusa i3. 1x PTFE tube (80mm).
1x SLS printed Extruder front.
1x SLS printed Extruder rear.
1x Bag with screws and bolts. 1x Fan shroud.
1x Mounting bracket.

MK2, MK2s, MK2.5 and MK3 without BMG

1x Nema17 Pancake stepper motor.
1x Stepper motor cable.
1x Shaft with 50T gear.
1x Thumbscrew.
2x Ball bearings.
1x 3x32mm shaft.
1x Sensor cover

MK2 and Mk2s

2x Needle bearing.
1x 3x20mm shaft.
1x Primary drive wheel (direct). 1x Secondary drive wheel (direct). 1x Sensor cover

Installation manual extruder upgrade for Bondtech_Prusa_i3 V1.1 | 3

## Mechanical Installation

## What you need

To install the upgrade you will need.
- M1.5- Hex Wrench
- M2.5- Hex Wrench
- Hobby knife with sharp tip or similar.

Recommended: Download and print out Bondtech’s PTFE fixture for precise measurement of the tube length. STL-file available at https://github.com/BondtechAB/Bondtech_Prusa_i3/tree/master/CAD-Files

## Preparation

Remove your old extruder. Use Prusa’s extruder assembly guide to reverse the steps if you need to. This kit will use a different motor, so you can unwrap the cables, remove your current motor to prepare for a new one.

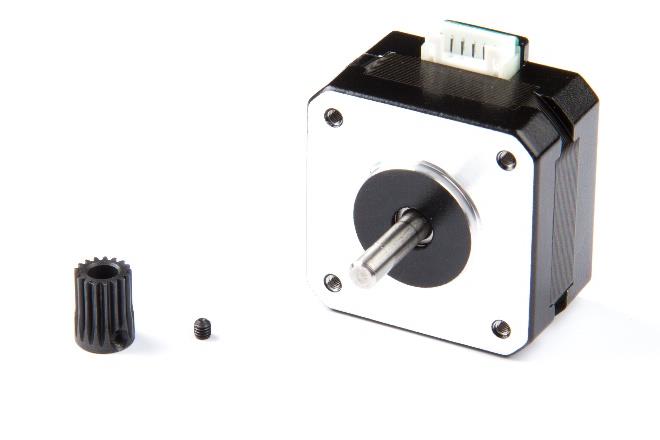
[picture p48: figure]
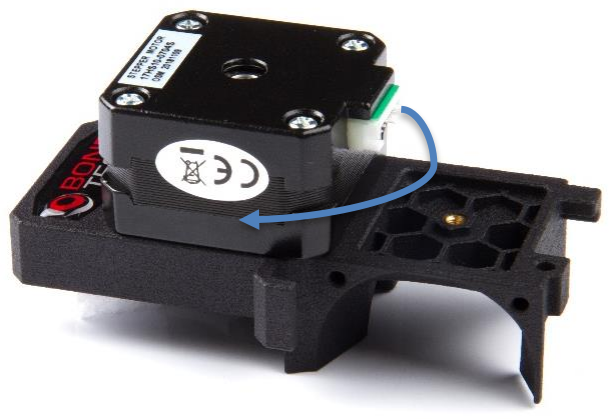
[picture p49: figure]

Installation manual extruder upgrade for Bondtech_Prusa_i3 V1.1 | 4
- Preparing your motor.
- Insert the M2x3 setscrew and slide the motor gear onto the shaft as oriented in the picture.
- Leave a 1-1,5 mm gap between the gear and the motor and tighten it using your 1,5mm Allen key.

Recommended: Use Loctite to secure the screw.

- Assembly the extruder front.
- Place the motor on the extruder front and orient the cable connection as you choose.
(Downwards or to the left.)

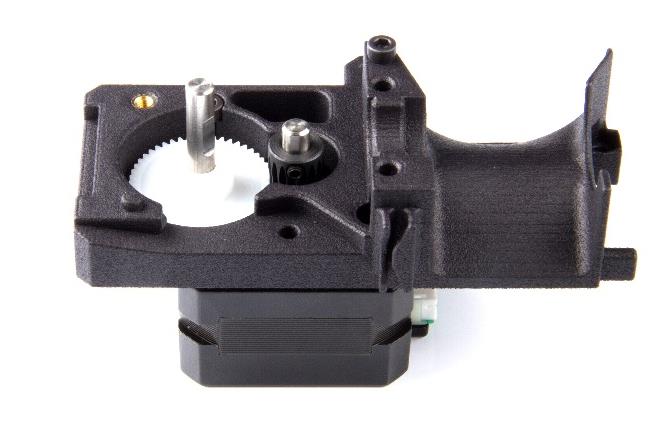
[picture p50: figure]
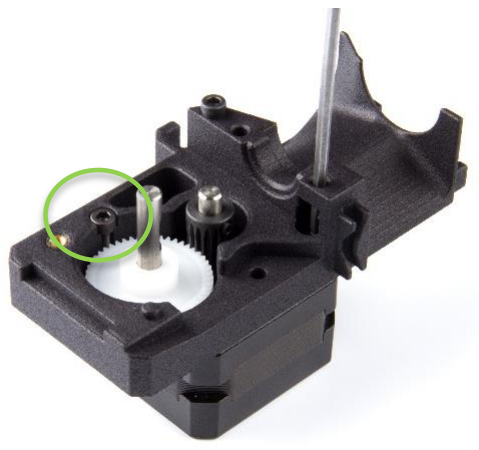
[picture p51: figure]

Installation manual extruder upgrade for Bondtech_Prusa_i3 V1.1 | 5
- Insert three M3 screws and loosely tighten them using a 2.5mm Allen key.
- M3x8
- M3x12
- M3x25
- Insert a ball bearing. Ensure it is fully pressed down into the slot.
- Insert the shaft with the white plastic gear into the bearing. Rotate the shaft to ensure correct alignment of the gears.
- Tighten the screws with
reasonable force.
- Important: Be careful
when tighten the M3x12
screw to avoid damaging
the pocket!

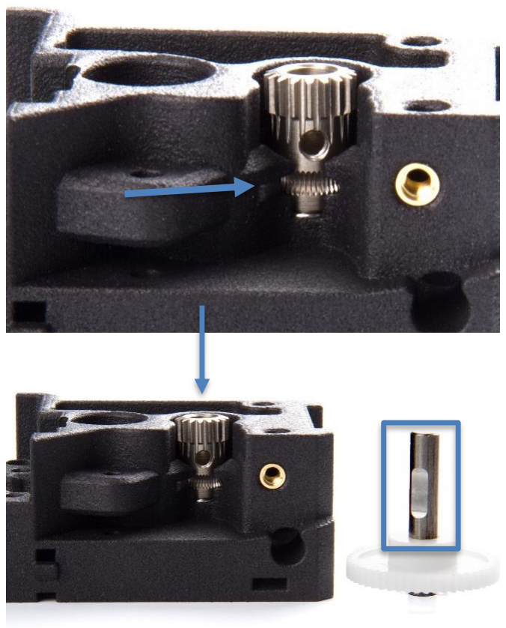
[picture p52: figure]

Installation manual extruder upgrade for Bondtech_Prusa_i3 V1.1 | 6
- Insert a square nut into the pocket.
- Prepare the extruder rear. Insert a ball bearing and press it down using a primary drive gear.
- If you are using the bear X-carriage remove hex cover plug by pushing it from the rear side. This hole is for a M3 nut.
- Press the primary drive gear down until the groves align with the filament path.
- Slide the shaft inside the drive gear. Note the orientation of the parts. The hole and the flat surface on the shaft must align.

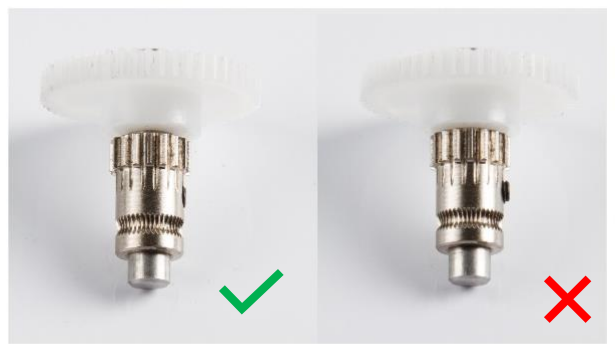
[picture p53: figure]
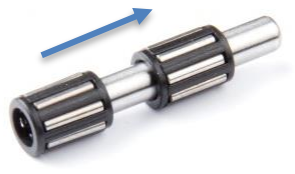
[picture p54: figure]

Installation manual extruder upgrade for Bondtech_Prusa_i3 V1.1 | 7
- Insert the M3x2 setscrew and tighten it with your 1,5 Allen key.

Important: Ensure the groves align with the filament path!

Recommended: Use Loctite to secure the screw.

Important: If the setscrew is not properly aligned with the flat surface it will stick out and start grinding on the
secondary drive gear when you start printing!
- Assemble the hinge.
- Slide the two needle bearings onto the 3x20 mm shaft.
- Use a small dab of lithium based grease to lubricate the bearings

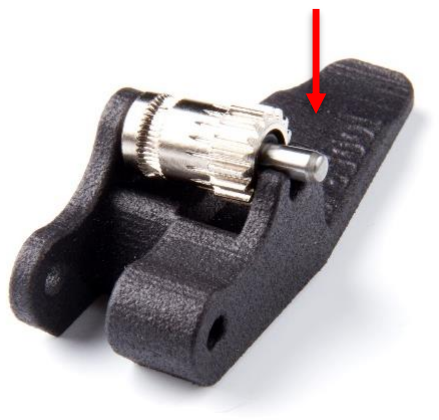
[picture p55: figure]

Installation manual extruder upgrade for Bondtech_Prusa_i3 V1.1 | 8
- Slide the shaft with the bearings through the secondary drive gear.
- Align the gear with the hinge as shown in the photo and press the shaft down until you hear the click.
- Carefully press the shaft in place using your 2.5mm Allen key.
- Put a small dab of lithium based grease on the gear section to reduce friction. Make sure that you do not get it on the drive section of the gear.
- Install the hinge to the extruder rear using the 3x32mm shaft.

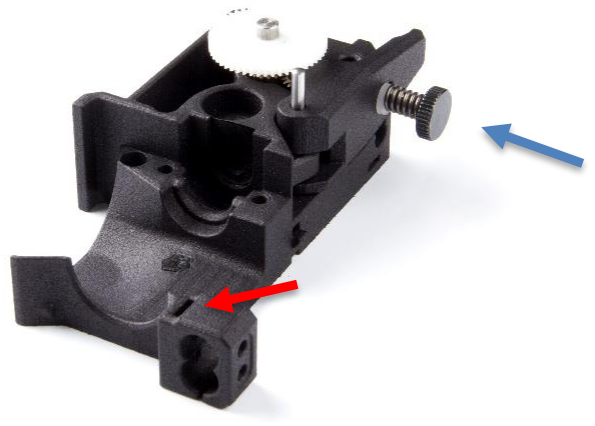
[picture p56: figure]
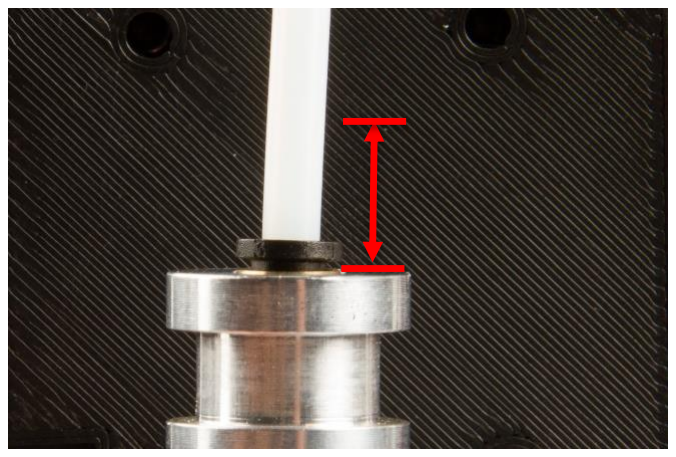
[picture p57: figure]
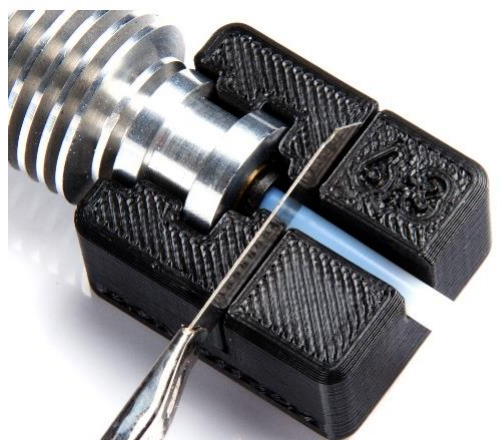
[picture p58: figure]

Installation manual extruder upgrade for Bondtech_Prusa_i3 V1.1 | 9
- Install the thumbscrew.
- If you are a MK2/s user
insert a square nut in the front pocket for the Pinda Probe.
- Prepare the HotEnd. Take the new supplied PTFE tube. Cut one of the ends according to Prusas recommendation, using a knife or a razor. Using this fixture (https://www.thingiverse.com/thing:3344656) will help. (Credits to Olof Ogland)
- Insert the newly cut end of the tube into the HotEnd.
- Cut the tube 6.3 mm from the top of the HotEnd. Save the
remaining piece for the sensor cover.
- Recommended: Use Bondtech’s cutting fixture for precise measurement. STL-file is
available at:
https://github.com/BondtechAB/Bondtech_Prusa_i3/tree/master/C AD-Files (https://github.com/BondtechAB/Bondtech_Prusa_i3/tree/master/CAD-Files)

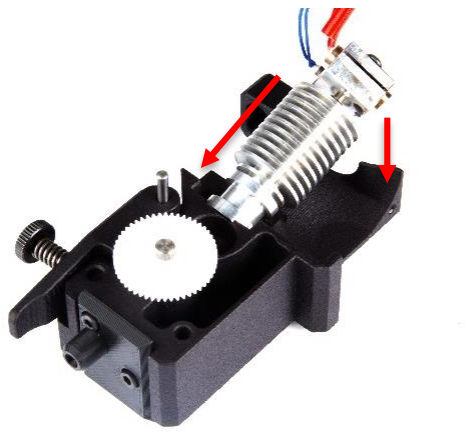
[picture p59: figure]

Installation manual extruder upgrade for Bondtech_Prusa_i3 V1.1 | 10
- Use a knife or razor to chamfer the inside of the tube for better filament guidance.

Important: Do not let any left over from the tube fall into the HotEnd we recommend you
remove the tube before
chamfer the inside!
- Insert a push fit clip between the HotEnd and the collet.
- Recommended: Add a small piece of tape, 5x20mm on the inner ring. The low friction between the parts may cause the HotEnd to rotate to easily when installed.
- Install the HotEnd into the extruder rear, angled as shown in the photo. And push it in place.


Installation manual extruder upgrade for Bondtech_Prusa_i3 V1.1 | 11
- Attach the front onto the rear part. Push the HotEnd upwards to align the neck correctly.
- Ensure everything is aligned and carefully clamp the parts
together.

Important: The parts should fit together easy. Do not use any excessive force!

- Install the extruder to your X-Carriage using three M3 screws.
- M3x40
- M3x45

Important: These screws are sized to use on your stock MK2,5/MK3 carriage or the
modified MK2/s carriage. If you have another carriage different screw length could be
necessary!
- Connect the cable to the motor and use the cable path to the left of the extruder for guidance.
- When connecting the cable to you board ensure the black cable is the top most cable or the motor will rotate the wrong way!

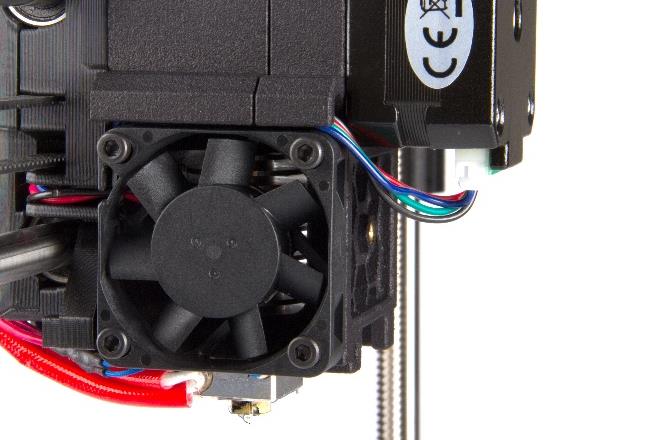
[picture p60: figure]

Installation manual extruder upgrade for Bondtech_Prusa_i3 V1.1 | 12
- Install your 40x40 fan using four M3x12 screws.
- Press down the hex nuts into the pockets of the mounting bracket.
- Install the mounting bracket and fan shroud using two M3x10 screw.
- M3x10
- Place two hex nuts into the slots on the mounting bracket and slide your 5015-blower fan down the fan shroud and mount it using two M3x20 screws.
- Place the cable in the channel on the right side of the extruder to help guide the way.

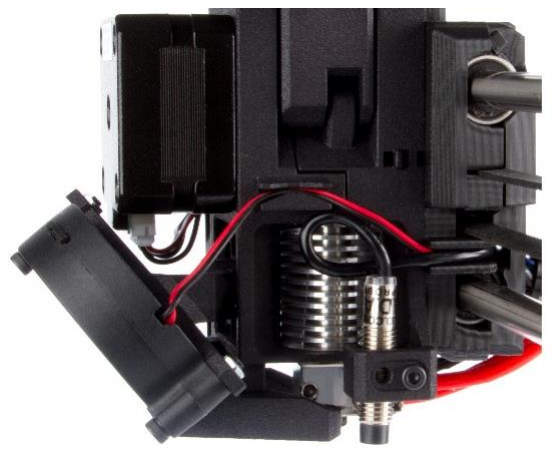
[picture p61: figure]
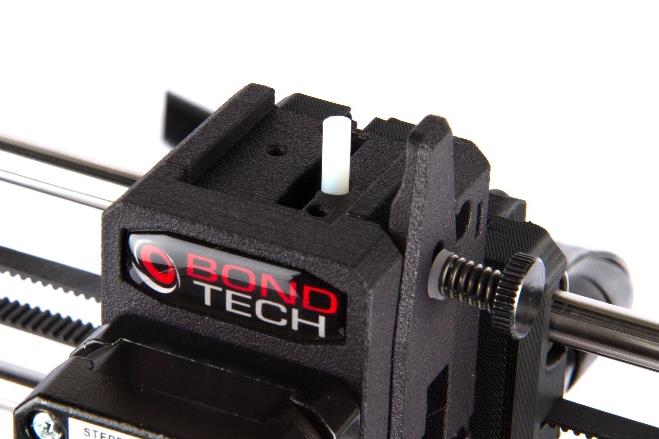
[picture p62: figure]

Installation manual extruder upgrade for Bondtech_Prusa_i3 V1.1 | 13
- The position of the P.I.N.D.A probe depends on your version of the printer. MK2/s users place the probe to right (Closer to the X-axis) MK2.5 and MK3 users place the probe to the left (furthest away from the X-axis).
- Optional P.I.N.D.A cable position. This technique is developed by Grégoire Saunier, creator of the Bear Extruder, to improve air flow and reduce turbulence. Check out his work here: (https://github.com/gregsaun)
- MK2.5, MK3 users insert a square nut into the right slot (MK2s in the left as shown earlier). Secure the P.I.N.D.A using a M3x16 screw.
- Square nut
- M3x16

Reminder: Adjust the height of the probe according to Prusa’s instructions.

- Cut a 14.5mm long piece of the left-over PTFE Tube and insert it into the filament path on top of the extruder.

Recommended: Before inserting the tube use a knife or razor to chamfer the inside of the tube for better filament guidance.

- If you have a filament sensor install it according to Prusa’s instructions.


Installation manual extruder upgrade for Bondtech_Prusa_i3 V1.1 | 14
- Place the sensor cover on top and fasten it using two M3x8 screws.

Installation manual extruder upgrade for Bondtech_Prusa_i3 V1.1 | 15

## Software Configuration

As the new extruder uses a gear reduction to create a high extrusion resolution and high torque the E-step value needs to be changed. The E-step value tells the printer how many steps to send to the motor for each mm of filament.

## Set new E-step value

The E-step value is set using a G-code file that you can download here: (https://github.com/BondtechAB/Bondtech_Prusa_i3/tree/master/GCODE)
These files are used to set the new E-step value on the printer. On MK2, MK2S and MK2.5 the E-step value should be 415 as it uses 16-bit microstepping, on MK3 it shall be 830 as it uses 32-bit microstepping, this is valid for standard 1.8-degree stepper motors, if a 0.9 degree motor is used the E-step needs to be doubled, so 830 and 1660.

Copy the file to the SD-card and put it in the printer, select to print the file and the new e-step value will be set and saved to the controller.

Good luck with your Bondtech feeder!

If you have any questions please first read the FAQ (http://www.bondtech.se/en/faq/). If the question still hasn’t been answered feel free to contact us by email or our online chat.

Repslagarvägen 3 J
33153 Värnamo
Sweden

e-mail: support@bondtech.se phone: +46702220193
paypal: payments@bondtech.se
web: www.bondtech.se
VAT-registration number: SE556995564301

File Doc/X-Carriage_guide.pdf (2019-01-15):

# X-Carriage guide

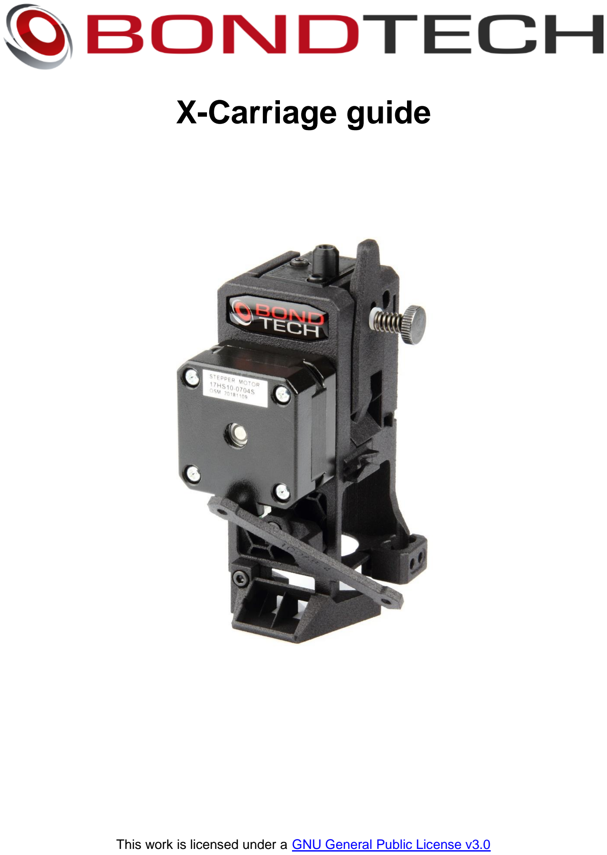
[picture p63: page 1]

This work is licensed under a GNU General Public License v3.0 (https://www.gnu.org/licenses/gpl-3.0.html)

X-Carriage guide for Bondtech_Prusa_i3 V1.0 | 1

## Table of Contents

Introduction | 1
Prusa | 2
Version: X-Carriage_MK3(R2) | 2
Bondtech | 3
Version: X-Carriage_Modded(R2)_for_Mk2(s) | 3
Bear | 4
Version: Bondtech_x_carriage_mk3 | 4
Zaribo | 5
Version: X-Carriage 2.31 | 5
Vecko | 6
Version: X-Carriage v2 | 6
Version: X-Carriage v2.6S_Mk3 | 7
Version: X-Carriage v2.61S_Mk2s | 8

## Introduction

This simple guide to show what fasteners you will need for some of the most popular X-Carriages. The Bondtech kit contains screws suited for the Original Prusa carriage, if you use another carriage different screw lengths and nuts could be necessary.

## Prusa


https://github.com/prusa3d

Version: X-Carriage_MK3(R2)

- M3x40
- M3x45

## Bondtech

https://github.com/BondtechAB/Bondtech_Prusa_i3

Version: X-Carriage_Modded(R2)_for_Mk2(s)


- M3x40
- M3x45


## Bear

https://github.com/gregsaun/bear_extruder_and_x_axishttps://www.thingiverse.com/pekcitron/designs

Version: Bondtech_x_carriage_mk3


- M3x10 x2 | • M3 hex nut x3
- M3x40 x3 | • M3 Square nut (Into extruder)

## Zaribo


https://github.com/Zaribo/Zaribo-MK3https://www.thingiverse.com/wschadow/designs

Version: X-Carriage 2.31

- M3x10 | • M3 hex nut.
- M3x30 | • M3 Square (Into extruder)
- M3x40 x2

## Vecko


https://www.thingiverse.com/vekoj/designs

Version: X-Carriage v2

- M3x8 | • M3 Square nut (Into extruder)
- M3x30
- M3x35
- M3x40

Version: X-Carriage v2.6S_Mk3


- M3x40
- M3x45


Version: X-Carriage v2.61S_Mk2s

- M3x40
- M3x45

If you have any questions please first read the FAQ (http://www.bondtech.se/en/faq/). If the question still hasn’t been answered feel free to contact us by email or our online chat.

Repslagarvägen 3 J
33153 Värnamo
Sweden

e-mail: support@bondtech.se phone: +46702220193
paypal: payments@bondtech.se
web: www.bondtech.se
VAT-registration number: SE556995564301

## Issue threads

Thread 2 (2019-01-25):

Unload filament MK3 prusa3d_fw_MK3_3_5_1.hex

Dutchy-79, 2019-01-25:
Hi Martin, (and other guys?)

I'm pretty happy with the print quality with the new Bondtech MK3 kit though there's one major thing.
When I unload filament it stays between the gears and if you are too slow opening the hatch it can get stuck inside.

For example, I unload PLA but want to load PETG so I heat up to 230C and hit unload, The it reverses quite slow (In my opinion which could be based on sound too much) and then it askes me to pull out quickly, Though it's stuck between the gears so you can almost lift the printer on it and the PLA starts to cool already.

What should I change (or can you ask Prusa to make a Bondtech option in the menu)

Regards,

Jasper

Dutchy-79, 2019-01-27:
I did some rough measurements and the gears on this version are about 5mm higher up in the design so instead of 80mm unload we should need 85mm unload command.

Dutchy-79, 2019-01-27:
Also the unload sequence seems slower.

Dutchy-79, 2019-02-01:
The mighty @codiac2600 aka Chris Warkocki made some firmware changes to improve unload.
https://github.com/codiac2600/Compiled-Firmware

Closed 2020-05-26.

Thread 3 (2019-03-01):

MMU2 version of MK3S filament sensor mod?

monglet, 2019-03-01:
Any chance of a top part for the latest update that incorporates the fixing for the festo coupler?

Pitterz, 2019-03-04:
X2.  It looks like an easy fix but the print would involve supports :(

Dutchy-79, 2019-03-04:
Depends on how you draw the part, make it bulky and you don't. https://www.thingiverse.com/thing:3461572
https://www.thingiverse.com/thing:3463618

ruedli, 2019-03-14:
when support for the MMU2S is needed, the detector needs to be triggered by door movement, which involves something totally different for the optical sensor part in addition to attaching the FESTO coupler to the extruder.

The Prusa MK3S / MMU2 compatible parts are here:
https://github.com/prusa3d/Original-Prusa-i3/blob/MK3S/Printed-Parts/STL/adapter-printer-mmu2s.stl

https://github.com/prusa3d/Original-Prusa-i3/blob/MK3S/Printed-Parts/STL/fs-cover-mmu2s.stl

and

https://github.com/prusa3d/Original-Prusa-i3/blob/MK3S/Printed-Parts/STL/extruder-idler-mmu2s.stl

Notice the lever on the idler needed to transfer the movement towards the IR filament detector !

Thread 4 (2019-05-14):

MK3S filament sensor stuck in loaded position

HMPoweredMan, 2019-05-14:
The actuation lever and ball bearing get stuck in the actuated position under the sensor. It does not return to the original position when filament is removed rendering it useless.

This appears to be due to the magnet in the lever being attracted to the M3 bolt used to connect the housing to the rest of the extruder. It could also be due to too much friction between the arm and the housing. This occurs even with the axis bolt is loose.

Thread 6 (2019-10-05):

Temperature Issue on mk3s with Mosquito

rcorgill, 2019-10-05:
Hopefully this is the right place to post this...I recently installed the Bondtech\Mosquito kit on my Mk3s along with slice engineering heater cartridge and slice engineering thermistor.  I flashed the 3.8.0 file named "bondtech_fw_MK3s-16_SE_HT-Thermistor_3_8_0.zip" and the firmware flashed successfully.  However I cannot print higher than 295 degrees....I confirmed with Bondtech support that the firmware (with HT-Thermistor in the file name) should have the correct tables to support the high temp thermistor but that doesn't look to be the case.   Most guides online for compiling the firmware are for the factory hotend\extruder so I'm not sure what to do...Any ideas?  Thanks

Tooke, 2019-12-09:
Confirmed the same issue with the same setup as above.

bondeus, 2019-12-12:
We also made versions to support Slice Engineering high temperature thermistor. We reduced the MINTEMP threshold to allow use in colder environments. The max temp was not changed. If you are an experienced and knowledgeable user you can change the HEATER_0_MAXTEMP parameter to fit your needs.

Pasted from: https://www.bondtech.se/en/knowledge-base/firmware-updates-for-prusa-i3/

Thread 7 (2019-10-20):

bondtech_fw_MK3s-16_3_8_0 Load/Unload issues.

Cub3squar3d, 2019-10-20:
Just installed the Bondtech upgrade on my Prusa Mk3s.
Everything looks fine, calibration completed without issues, test cube is nice.
The problem is that the load and unload sequences have the wrong length, and the filament doesn't quite reach the nozzle during load, and gets stuck after the gears during unloads, forcing a release of the thumbscrew to completely unload.

Cub3squar3d, 2019-10-20:
My bad, manually updating the e-steps to 415 through console is required since it's not written to eeprom by the flashed firmware.

Closed 2019-10-20.

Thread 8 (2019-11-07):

Z_MAX_POS issue on MK2.5s

falconrh, 2019-11-07:
I am having a problem with the XYZ Calibration tests after installing the BondTech Extruder on my Prusa MK2.5s. The Extruder travels down to 5mm and stops. (~1mm above the bed)  When I looked at the Z_MAX_POS value in the source code (1_75mm_MK25S_Bondtech-RAMBo13a-E3Dv6full.h), I see that it is set to 210 not 205.  My understanding is the correct value is 205.

lejo1512, 2019-11-07:
I've uploaded correct files now.
Thanks for reporting this issue!

falconrh, 2019-11-07:
Yes, that fixed my issues.  Thanks for the quick turnaround :)

Closed 2019-11-07.

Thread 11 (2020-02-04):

Where shall I place the MK3s "#elif define" changes?

elektronchika, 2020-02-04:
Dear Bondtech team,

thank you providing all the changes that you have implemented in Prusa firmware. I only cannot understand where I have to place the last 3 changes for MK3s firmware? I would be very appreciative if you let me know.

Thank you and kind regards,
Lazar

lejo1512, 2020-02-04:
These changes are made in mmu.ccp during "mmu_load_to_nozzle()"and  "can_load()".

dmnkhhn, 2020-05-19:
Hello!

I have to make the changes from the "MK3s Mosquito with high temperature thermistor (SliceE_HT)" part of the documentation in the mmu.cpp of firmware 3.9.0 but I can't find where to put them.

Those lines are:
```
#elif defined(BONDTECH_MOSQUITO) current_position[E_AXIS] += 70; //Bondtech_Mosquito 70mm from drive gear to melt zone
#elif defined(BONDTECH_MOSQUITO) current_position[E_AXIS] -= 62; // Pull back 62mm, 8 mm below drive gear
#elif defined(BONDTECH_MOSQUITO) current_position[E_AXIS] += 23.4f; //Bondtech Mosquito 9 mm longer t melt zone
#ifdef BONDTECH_MOSQUITO current_position[E_AXIS] += 16.4f; //2mm further through Mosquito heat block
```

Thanks for any help. :-)

3d-gussner, 2020-05-19:
Checkout https://github.com/Zaribo/Zaribo-Firmware there you can compare it with Prusa and see the changes you need to make.
Or you compile this firmware.

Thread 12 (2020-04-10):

MK2.5s Mosquito with high temperature thermistor (SliceE_HT) firmware not showing right temperature

RiotShooter75, 2020-04-10:
I flashed this firmware to my Prusa and my printer is not showing the correct temperature. Thouhgts?

jgrg1, 2020-04-19:
Hi, I have exactly the same issue, exactly the same build (MK2.5S with Mosquito hotend and SE HT thermistor). I've dug through the firmware codebase, and I believe that it's using the correct table in thermistortables.h with TEMP_SENSOR_0 = 800 from the variants\1_75mm_MK25S_Bondtech-RAMBo13a-SliceE_HT-Mosquito.h file.

Is there a solution to this?

RiotShooter75, 2020-04-19:
Apparently Prusa broke something in a recent update/the rambo used on the MK2 variants has issues with the Slice Thermistor. I had to move back to using an E3D thermistor on my Prusa.

3d-gussner, 2020-04-19:
Please checkout vertigo235 fork of prusa firmware... I think he got it working.
Other option is zaribo github fork.

Panayiotis-git, 2020-04-19:
It seems like the build for the mk25s has not used the definition TEMP_SENSOR_0 = 800 but the TEMP_SENSOR_0 = 5.

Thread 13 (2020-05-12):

M600 for new 'Color Print' results in printer pausing

gummerch, 2020-05-12:
I'm trying to use the new 'Color Print' functionality in Prusalicer 2.2.0. Instead of instituting the expected color change the printer pauses and turns the heat off to the extruder. Is it possible there is a conflict with the firmware?
[MMU Test V1.zip](https://github.com/BondtechAB/Bondtech_Prusa_i3/files/4617323/MMU.Test.V1.zip)

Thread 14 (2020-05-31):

Fan shroud backside cooling

elektronchika, 2020-05-31:
Dear Bondtech team,

I'm experiencing pour cooling on the back of the printed object. This is particularly visible in small objects printed in PLA, ASA, PETG and CPE (the issue is present with all filaments I've tried). There are a lot of similar complaint in Reddit for example.

Are you considering updating the fan shroud in the near future to achieve better cooling? I think that the current design cools also the heatblock from front and the side opening are blowing the heatbed, but the not nozzle.

Thank  you!
Lazar

timhoover73, 2022-01-24:
Hey Lazar,

I just upgraded my Prusa i3 Mk3S to a Bondtech extruder.  I created my own part cooling shroud and posted to Thingiverse here: https://www.thingiverse.com/thing:5214069
[New_Part_Cooling_Shroud_BMG_1.7.zip](https://github.com/BondtechAB/Bondtech_Prusa_i3/files/7922465/New_Part_Cooling_Shroud_BMG_1.7.zip)

Good luck,
Tim

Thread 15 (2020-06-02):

Extruder runs in reverse

tdshank84, 2020-06-02:
After BMG upgrade to my i3 Mk3s, the extruder runs in reverse.

All connections are only able to be made in one direction (updated cables)

What needs to be corrected on this?

This line needs to be made from DIR 1 to DIR 0

#define INVERT_E0_DIR 1   // for direct drive extruder v9 set to 1, for geared extruder set to 0

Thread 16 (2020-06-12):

PTFE Cutter for the BMG Extruder 5mm

Nandox7, 2020-06-12:
AS the tittle says, there is a nice one for the 6.3mm of the prusa upgrade and it would be cool to have the same for the BMG Extruder 5mm.

Thanks

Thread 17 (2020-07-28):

Why is the source in a zip file and not in the repo?

casonclagg, 2020-07-28:
I assume this is a pseudo-fork of Prusa Firmware....

1) Shouldn't this be an actual fork so that it can pull in the new features and bug fixes that Prusa releases?
2) It'd be nice to maintain the source outside of a zip file so that you can track changes, make forks, and PRs.
3) It would also be nice to manage versions with branches instead of folders.

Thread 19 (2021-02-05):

XYZ Calibration issue

Emili1116, 2021-02-05:
Hello !

I'm using a MK3S with Bondtech extruder and Bear X axis, when performing a XYZ calibration process (Bondtech firmware 3.9.3-4117) the PINDA probe is offcentered from the first calibration point by 5-10mm in the negative X value, looks like the PINDA probe's offsets aren't correct for this setup. The first time, findind the first calibration point worked for some reason, then the print head crashed against its maximum X postion. Weird.

I've set the Z offset of the PINDA probe using a zip tie, everything runs smoothly, exept for this issue.

X, Y and Z home offsets are correct.

Thanks !

Emilien.

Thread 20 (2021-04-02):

Prusament PC Blend

Bohmut, 2021-04-02:
Printer: Prusa MK3S
Intstallied extruder upgrade kit + carriage upgrade.

After the upgrade I'm using these BMG profiles https://prusaslicerprofiles.com/

Results: PLA and PETG prints are awesome, the quality is significantly better.

Problem: Prints made with PC Blend Fillament (Prusament PC Blend) now looks much worse and I can't find a proper profile for this kind of Fillamant.

Can anyone help?

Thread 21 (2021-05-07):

GCode interpreted incorrectly

zlilly, 2021-05-07:
Using FW393-Build4117-Bondtech-MK3S-16-EINSy10a-E3Dv6full from this repository, extra movements are added that are not specified by the gcode which severely impact print quality. The first attached picture is a screen shot of my test gcode in prusa-gcodeviewer. As you can see, at no point should the extruder pass over the center of the cube in an x pattern. In the photographs attached, the left was printed using the firmware specified from this repository and the right was printed using firmware built directly from the v3.9.3 branch of the prusa3d repository. The only thing I changed in the firmware from the prusa repo was the E steps per unit (M92 E415). The test cube that I photographed was sliced with Cura 4.8 but the same problem also occurs when using prusa slicer v2.3.1. I have attached the gcode file but any should yield the same result. The printer is a Genuine Prusa MK3s with the bondtech upgraded extruder and original e3dv6 hotend. I use repetier-server for remote printing but that should not affect gcode interpretation as it simply passes the gcode to the serial interface.

[cube.gcode.txt](https://github.com/BondtechAB/Bondtech_Prusa_i3/files/6438552/cube.gcode.txt)
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

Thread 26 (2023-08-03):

MMU3 MK3S/+ Bondtech Bear Upgrade compatability

taz43mca, 2023-08-03:
I am looking at getting the Prusa MMU3 for my Bear MK3S with the Bondtech extruder. Prusa has no experience with checking compatability of this configuration. Has anyone looked at this configuration? I know I will have to design a mounting due to the 2040 V frame but my concern is with the extruder (x Axis) configuration.

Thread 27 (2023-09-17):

After mounting, X endstop is not touching

nbouayad, 2023-09-17:
Hello,
On a Prusa MK2,the extruder rear cables prevent the x-endstop to be pushed, as seen in the attached pictures :

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

What can be done??!
Thanks,

lejo1512, 2023-09-18:
I assume you are using "X-Carriage-modded(R2)__for_MK2(s)" with the extended arm to hit the switch?
Is the

With the R3 cable-holder design the sleeve and zip-ties needs to be properly tightened around the cables.
The cable should be within the geometry of the cable-holder.

You could try the MK2.5 version of the cable holder, gives some more space around the frame:
https://github.com/prusa3d/Original-Prusa-i3/blob/MK2.5/Printed-Parts/stl/cable_holder.stl

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
(From Prusa MK2.5 assembly guide)

nbouayad-wincomplm, 2023-09-18:
@lejo1512, thank you for your answer.
Yes, I am using the modded R2 for MK2(s).
I will try the MK2.5 version of the cable holder and come back to you.
Kind regards,

nbouayad, 2023-09-20:
@lejo1512, using the MK2.5 cable holder solved the situation!!
Thanks again!

Closed 2023-09-20.

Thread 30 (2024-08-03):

Layer shift after pause or filament swap

thetoadsage, 2024-08-03:
Currently running an mk3s+ with the bondtech bmg upgrade. Using newest 3.14 bondtech firmware. While printing if I execute a pause or filament swap, when the print resumes it is always shifted back about 1mm in the y axis. I have seen others in Prusa forums with the same issue and it seems the common denominator is bondtech firmware

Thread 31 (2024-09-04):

[Request] Prusa i3 MK3S/+ with MK4 10mm Z-Axis and Bondtech BMG IDGA Extruder

SpankyDevil, 2024-09-04:
Hi can I please request that someone makes this extruder compatible with an upgraded Prusa i3 MK3S/+ with MK4 10mm Z-Axis

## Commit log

2019-03-01 Create MK3s Sensor Add-On
2019-10-23 hotend variants for mmu2s + MINTEMP threshold for SliceE-HT
2020-05-27 FW390-Build3922
    fix current pos during xyz cal
2024-02-26 Bondtech LGX for MK3S & Mosquito
    [LGX X-carriage for MK3S & Mosquito.STEP]
